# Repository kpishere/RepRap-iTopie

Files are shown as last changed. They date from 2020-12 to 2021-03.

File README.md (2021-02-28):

## Notes on this branch

I'm updating the build to accomodate parts readily available today.  Also making simplifications by design changes for ordering.

Changes include :  

- Pockets for screws that enable use of maximum 20mm screws (some were 30mm and these don't come in sets) 
- Adjust y-carrage to accommodate a 170mm x 170mm build heat plate screw hole pattern (heat plate is actually 235mm x 235mm)
- Adjust X,Y,Z sizes so that I only need 400mm rods and 400mm leadscrews (this was only 20mm or 40mm changes, why not that from beginning?)
- caviate: Notice that the Y-plane frame has pockets on one side and _should_ have the logo cut out on the other side but ... I'm not flipping this over to cut pockets, so the logo would be on the wrong side if it is cut like this.  Maybe don't cut the logo, rather 3D print it as a test and stick it on later if you want that.

A wiki page on the build milestones for the [iTopie400+](https://github.com/kpishere/RepRap-iTopie/wiki/General-RepRap-iTopie-build-experience-and-details-of-significance).

## [RepRap iTopie](http://reprap.org/wiki/ITopie)
Here you will find all the sources files for the [RepRap iTopie](http://reprap.org/wiki/ITopie).<br>The [build manual](http://reprap.org/wiki/ITopie_Build_Manual), [bill of materials](http://reprap.org/wiki/ITopie_Buyers_Guide) and other information is on the [RepRap wiki](http://reprap.org/wiki/ITopie).<br>Thank you.



## Highly customizable [frame generator](https://github.com/lautr3k/RepRap-iTopie/tree/dev/scad)

iTopie frame generator

## DXF [build tool](https://github.com/lautr3k/RepRap-iTopie/tree/dev/build)
Builder to create a clean layered DXF from (your custom) OpenSCAD source files.
iTopie DXF build tool
Generated DXF in CamBam

## Some pictures












## Looking for an extruder? Try the [Wade L3K Extruder](https://github.com/lautr3k/Wade-L3K).




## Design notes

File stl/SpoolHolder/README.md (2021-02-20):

Filler - The Customizable Filament Holder that fills your printer! by HugoHuge on Thingiverse: https://www.thingiverse.com/thing:3020026

The above release has been modified to use 5mm X 9 mm bearings (these are extra ones that come with a Titan Areo hot end assembly).

Cut parts have also been made if you wish to have two infil types in your print for those sections.

au: kpishere

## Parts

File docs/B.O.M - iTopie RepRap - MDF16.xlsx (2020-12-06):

Qty | Part name | Prix TTC (CHF) | Fournisseur
 | Wood
1 | MDF 16mm ~0.5m2 - Ex.: 860 x 580mm | 30 | Do-it (migro)
 | Wood screws
12 | 3.5 x 45mm | 1 | Bricovis
 | Metric screws
2 | M3 x 12mm |  | Bricovis
10 | M3 x 20mm |  | Bricovis
13 | M3 x 25mm |  | Bricovis
2 | M3 x 30mm |  | Bricovis
1 | M5 x 20mm |  | Bricovis
1 | M5 x 25mm | 8 | Bricovis
 | Washers
24 | M3 Washer - 3.2/7/0.5 |  | Bricovis
8 | M5 Washer - 5/8/1 |  | Bricovis
0 | M5 Washer - 5/12/0.5 | 3 | Bricovis | old version
 | Metric nuts
15 | M3 Nut |  | Bricovis
2 | M5 Nut - Nylock |  | Bricovis
2 | M8 Nut | 2 | Bricovis
 | Bearings
2 | 605ZZ Bearing | 2 | ebay
12 | LM8UU Linear bearing | 25 | reprapworld
 | Motor
5 | Nema17 - 1.8° / 4.8 kg/cm | 60 | reprapworld
 | Pulleys
2 | GT2 Pulley - 20 Theet | 8 | reprapworld
 | Belts
1 | GT2 Belt - 800mm | 5 | reprapworld
1 | GT2 Belt - 900mm | 5 | reprapworld
 | Flexible coupler
2 | 5/8mm Flexible coupler | 6 | reprapworld
 | Smooth rods
4 | D=8, L=380mm | 6 | reprapworld
2 | D=8, L=400mm | 3 | reprapworld
 | Threaded rods
2 | M8, L=360mm | 5 | Do-it (migro)
 | Electronics
1 | Smoothieboard 4XC | 130 | uberclock
1 | 30x30mm Fan | 3 | reprapworld
2 | 40x40mm Fan | 6 | reprapworld
1 | Power supply 12V - 30A | 25 | reprapworld
3 | Microswitch | 1.5 | conrad
1 | Heatbed MK3 | 20 | reprap.me
1 | Wiring | 10 | conrad
1 | Hotend Hexagone | 40 | reprapdiscount
 | Uncategorized
28 | Zip ties | 2 | conrad
 |  | TOTAL
 |  | 406.5

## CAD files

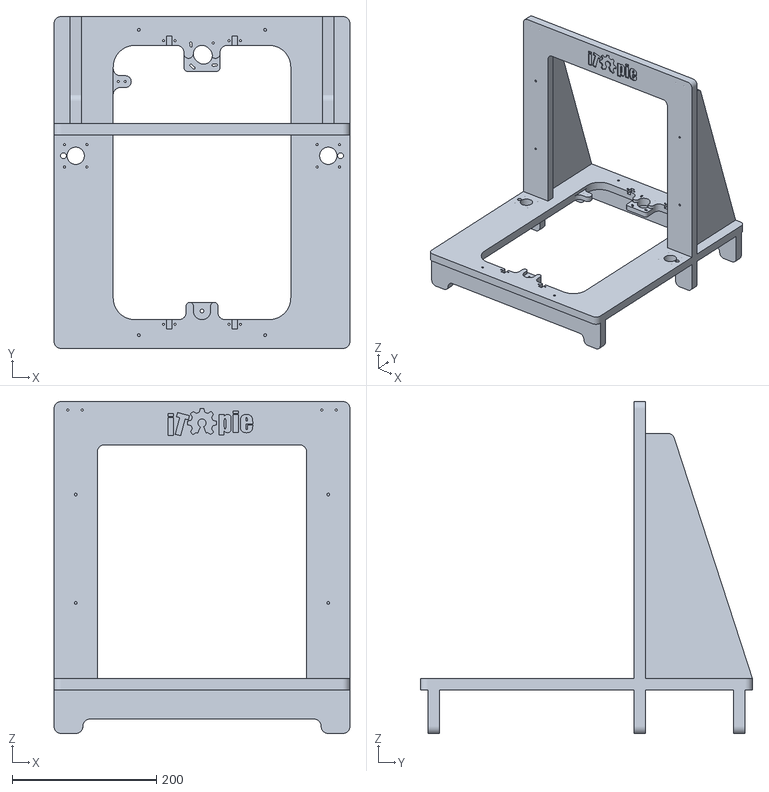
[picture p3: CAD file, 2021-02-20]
stl/main_assembled.stl
410.0 x 460.0 x 460.0

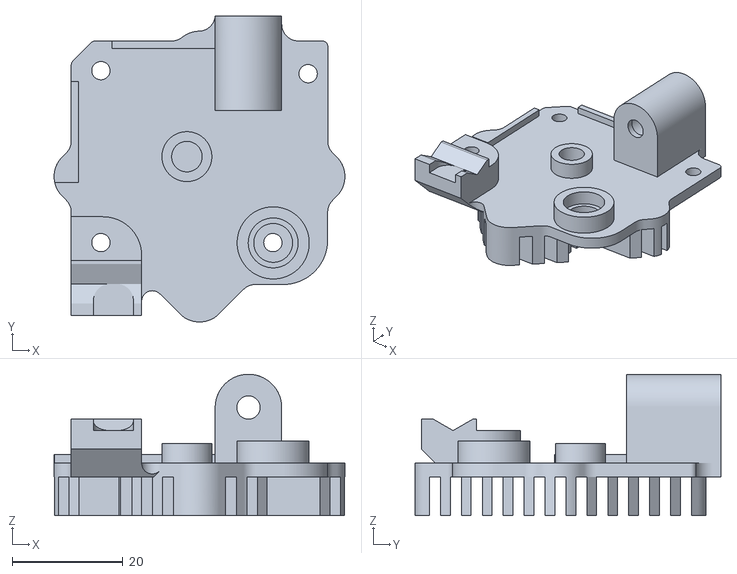
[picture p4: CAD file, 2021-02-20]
stl/Titan-Aero-Assembly_HotEnd.stl
52.4 x 55.2 x 25.5

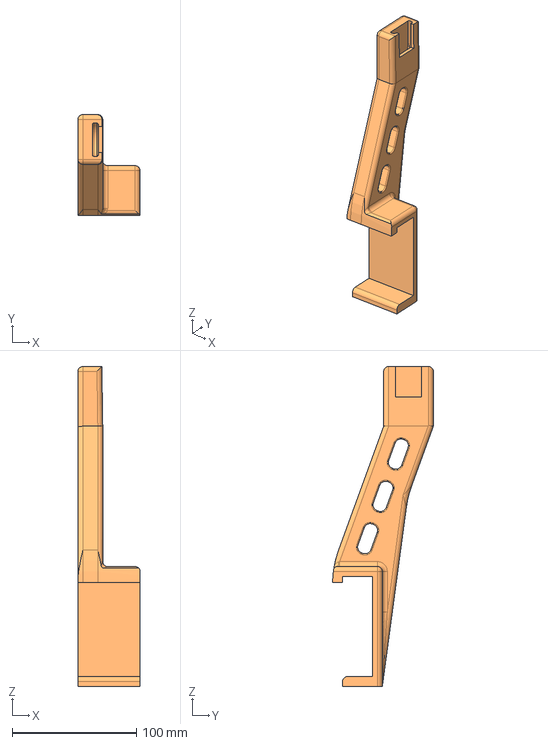
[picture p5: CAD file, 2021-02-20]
docs/Filler+-+The+Customizable+Filament+Holder+that+fills+your+printer!/files/FillerAnetA8Source.step
50.0 x 81.0 x 257.2 mm

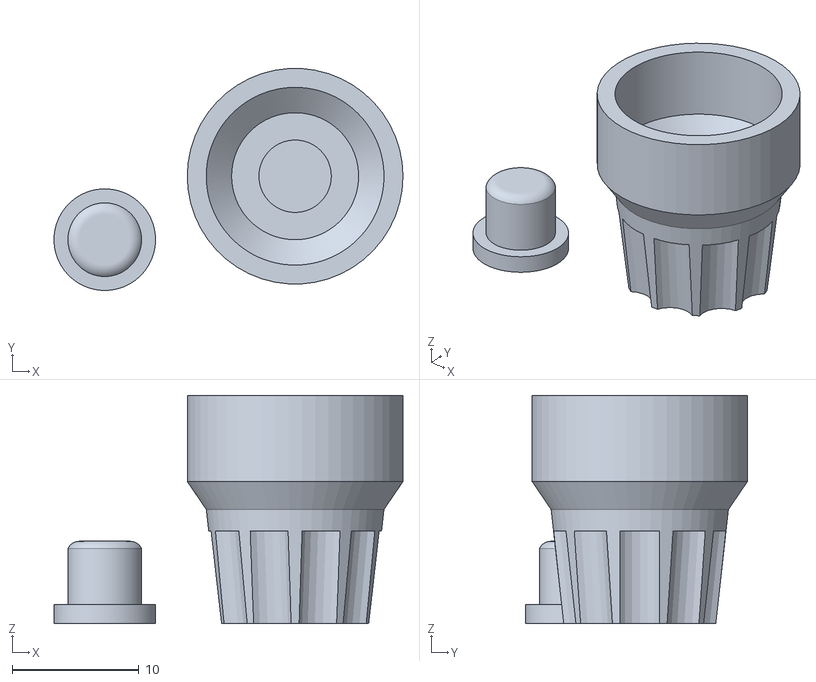
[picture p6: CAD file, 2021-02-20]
stl/AZSMZ 12864 Panel/Knob_v3.stl
27.5 x 17.5 x 18.0

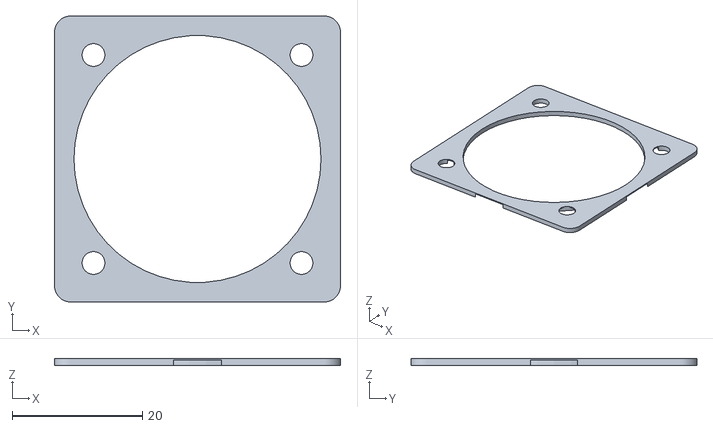
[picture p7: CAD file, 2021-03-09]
stl/damper_fan_mount.stl
44.0 x 44.0 x 1.00

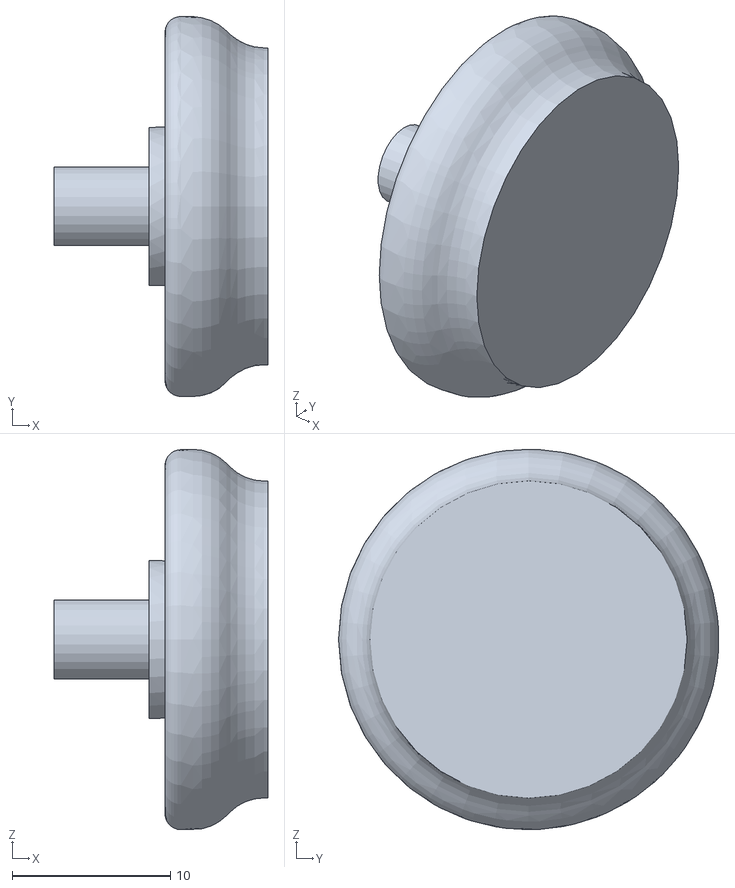
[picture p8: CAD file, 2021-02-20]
stl/SpoolHolder/SpoolRollerSection.stl
13.5 x 24.0 x 24.0

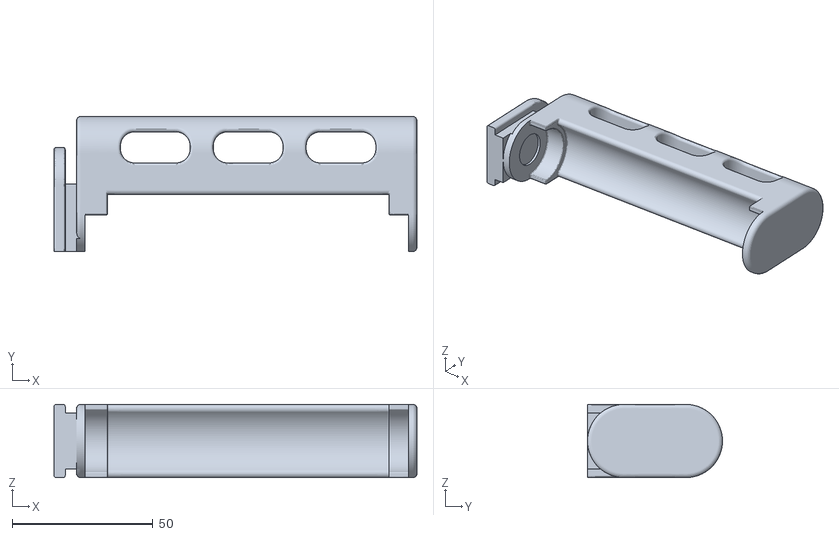
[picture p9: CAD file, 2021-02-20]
docs/Filler+-+The+Customizable+Filament+Holder+that+fills+your+printer!/3DPNFilHoldGuide.stl
129.0 x 48.0 x 26.0

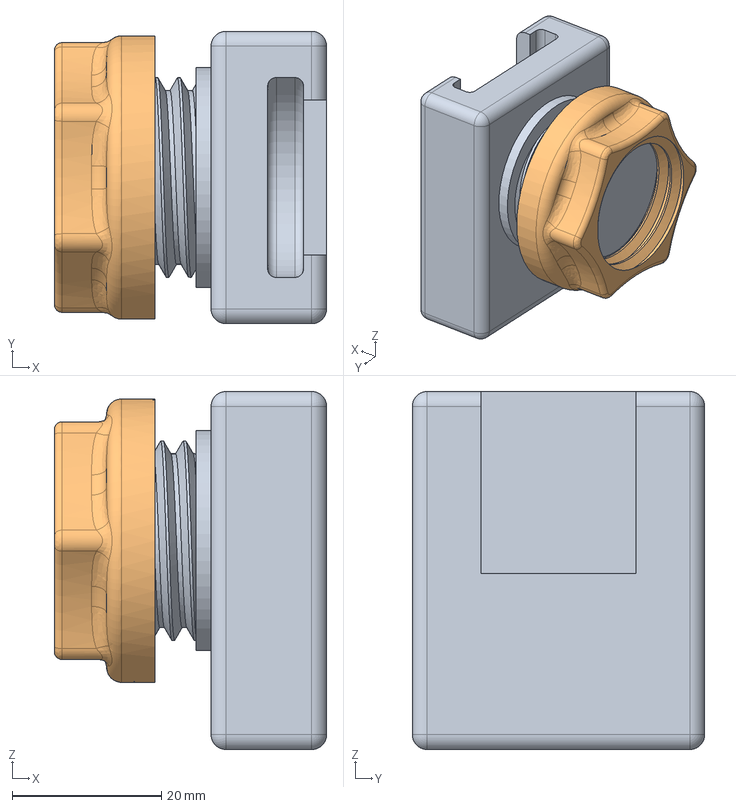
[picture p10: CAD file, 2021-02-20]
docs/Filler+-+The+Customizable+Filament+Holder+that+fills+your+printer!/files/FillerCR10-Ender3Source.step
36.5 x 39.2 x 48.0 mm

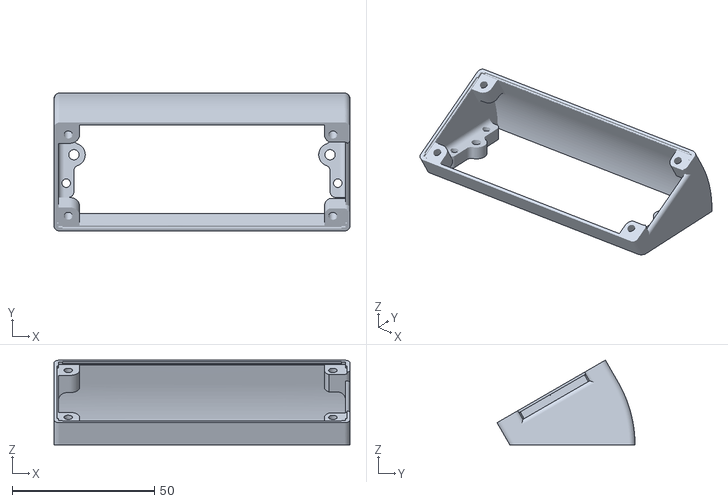
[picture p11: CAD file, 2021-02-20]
stl/AZSMZ 12864 Panel/Display_SD_Base.stl
104.0 x 48.5 x 29.8

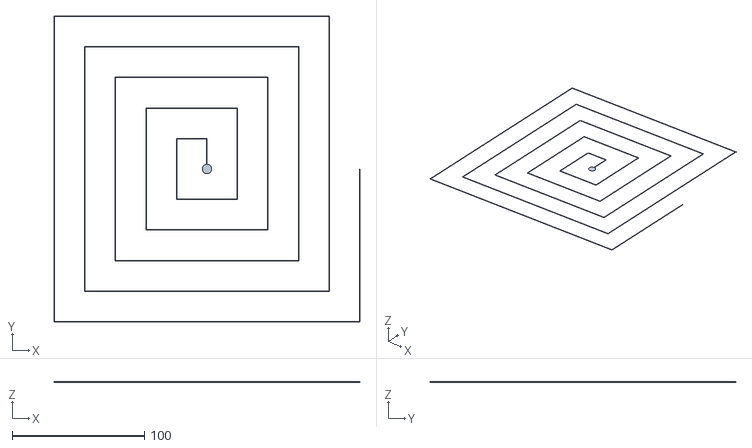
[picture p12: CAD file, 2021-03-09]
stl/bed_test.stl
231.2 x 231.2 x 0.2

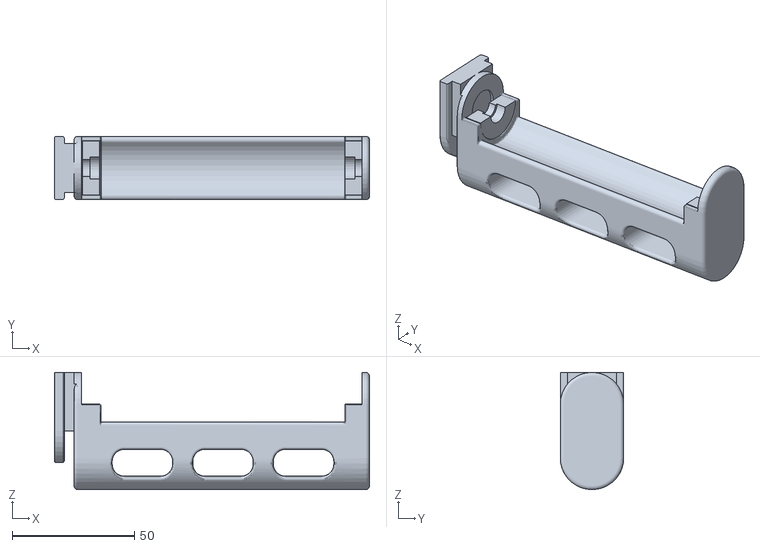
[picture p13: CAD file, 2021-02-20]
stl/SpoolHolder/SpoolBrace.stl
129.0 x 26.0 x 48.0

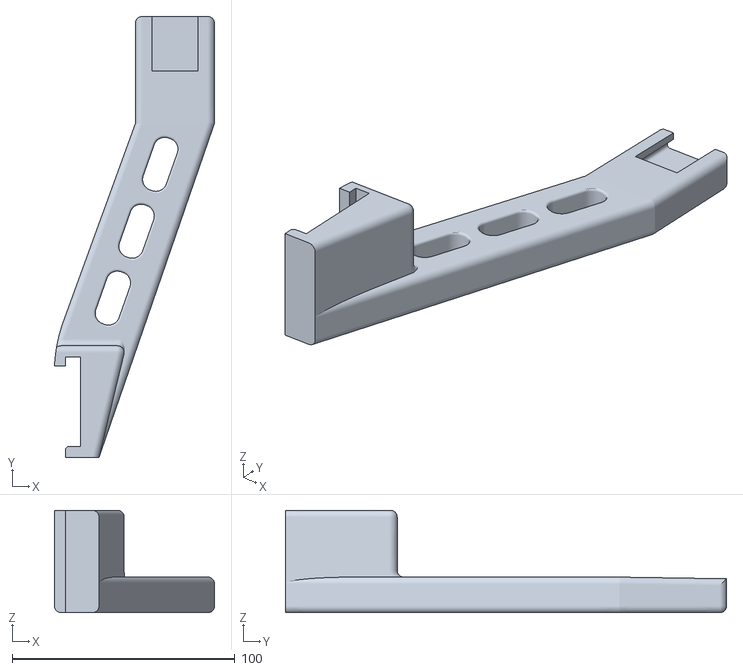
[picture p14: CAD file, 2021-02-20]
docs/Filler+-+The+Customizable+Filament+Holder+that+fills+your+printer!/FillerBracePrusaI3Mk1-2-3.stl
71.9 x 198.1 x 46.0

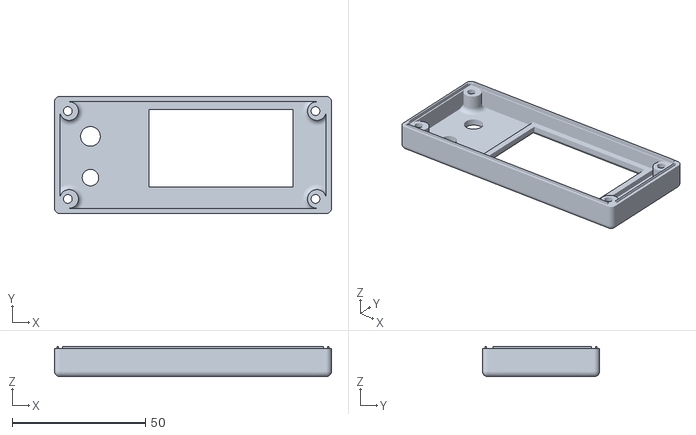
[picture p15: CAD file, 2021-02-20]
stl/AZSMZ 12864 Panel/Display_Front.stl
104.0 x 44.0 x 11.3

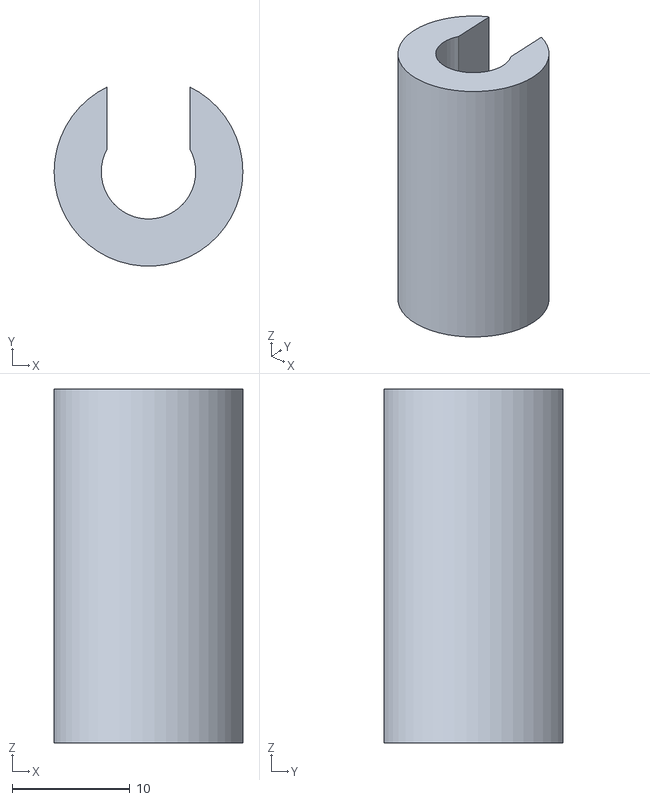
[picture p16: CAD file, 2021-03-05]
stl/clip-on-endstop-spacer.stl
16.0 x 15.2 x 30.0

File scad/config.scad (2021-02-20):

// iTopie RepRap - Configuration
//
// @version 1.0.1
// @license GPLv3
// @docs    http://reprap.org/wiki/ITopie  
// @sources https://github.com/lautr3k/RepRap-iTopie 
// @author  Sébastien Mischler <skarab>
// @author  http://www.onlfait.ch
//
$fn = 50;

// ---------------------------------------------------------------- //
// output settings
// ---------------------------------------------------------------- //
// output version
// 0 : CNC milling (default)
// 1 : Laser cutting
output_version = 0;

// output mode
// 0 : 2D preview (default)
// 1 : extruded view (slow)
// 2 : export first layer (plates)
// 3 : export second layer (pockets)
// 4 : build preview (slow)
output_mode = 0;

// output type
// 0 : all parts
// 1 : plate 1 (horizontal_plate, y_carriage, feet)
// 2 : plate 2 (vertical_plate, triangles, feet)
// 3 : horizontal_plate
// 4 : vertical_plate
// 5 : y_carriage
// 6 : triangle
// 7 : feet
output_type = 0;

// parts margin (mode : 0-3)
parts_margin = 10;

// ---------------------------------------------------------------- //
// drawing settings
// ---------------------------------------------------------------- //
sheet_thickness = 16;                    // raw sheet thickness
pockets_depth   = 6;                     // pockets depth
pockets_color   = "RoyalBlue";           // pockets color
connector_size  = [20, sheet_thickness]; // pockets/fingers [width, height]

// ---------------------------------------------------------------- //
// shortcuts
// ---------------------------------------------------------------- //
m3_screw_radius = 1.5;
m4_screw_radius = 2;
m4_washer_radius = 4;
workpiece_x = 1220;
workpiece_y = 610;

// ---------------------------------------------------------------- //
// horizontal plate
// ---------------------------------------------------------------- //
horizontal_plate_width         = 410;              // 
horizontal_plate_height        = 460;              // 
horizontal_plate_borders       = [40, 82, 40, 82]; // borders weight       [top, right, bottom, left]
horizontal_plate_outer_corners = [10, 10, 10, 10]; // outer corners radius [topLeft, topRight, bottomRight, bottoLeft]
horizontal_plate_inner_corners = [30, 30, 30, 30]; // inner corners radius [topLeft, topRight, bottomRight, bottoLeft]

// y motor mount
y_motor_mount_width   = 50;              //
y_motor_mount_height  = 36;              //
y_motor_mount_corners = [5, 5, 10, 10];  // corners radius [topLeft, topRight, bottomRight, bottoLeft]
y_motor_mount_angle   = 8;               // motor rotation angle (belt tensionner) 0 = disabled
y_motor_holes_radius  = m3_screw_radius; // y motor screw holes radius

// z_motor mount
z_motor_mount_margin  = 8;     // between the "motor" and the "z_plate" (border to border)
z_motor_mount_spacing = undef; // between the two motor mount (axis to axis) [undef = auto]

z_motor_holes_radius = m3_screw_radius; // z motor screw holes radius

// z rods
z_rod_spacing = 17; // between the "motor" and the "z rod" (axis to axis)
z_rod_radius  = 4;  // z smoothe rod radius

z_rod_holder_holes_radius  = m3_screw_radius; // z rod top holder holes radius
z_rod_holder_holes_margin  = [12, 6];         // [from the top frame border, between the z rod and the first holder hole (axis to axis)]
z_rod_holder_holes_spacing = 20;              // between the two holder holes (axis to axis)

// y idler mount
y_idler_mount_width       = 44;             //
y_idler_mount_height      = 24;             //
y_idler_mount_corners     = [5, 5, 10, 10]; // corners radius [topLeft, topRight, bottomRight, bottoLeft]
y_idler_mount_hole_radius = 2.5;            // y idler bearing hole radius

// y idler pocket
y_idler_pocket_width   = undef;                 // idler pocket width [undef = auto]
y_idler_pockets_height = y_idler_mount_height;  // idler pocket height

// y endstop mount
y_endstop_mount_width    = 25;                 //
y_endstop_mount_height   = 16.4;               //
y_endstop_mount_corners  = [8.2, 8.2, 10, 10]; // corners radius [topLeft, topRight, bottomRight, bottoLeft]
y_endstop_mount_position = 82;                 // from the frame top border to the endstop top border

// ---------------------------------------------------------------- //
// vertical plate
// ---------------------------------------------------------------- //
// vertical plate
vertical_plate_width         = horizontal_plate_width;  // outer width
vertical_plate_height        = horizontal_plate_height; // outer height
vertical_plate_borders       = [60, 60, undef, 60];     // borders weight       [top, right, bottom, left]
vertical_plate_outer_corners = [10, 10, 10, 10];        // outer corners radius [topLeft, topRight, bottomRight, bottoLeft]
vertical_plate_inner_corners = [10, 10, 10, 10];        // inner corners radius [topLeft, topRight, bottomRight, bottoLeft]
vertical_plate_position      = undef;                   // y position from the horizontal plate bottom border      

// ---------------------------------------------------------------- //
// logo
// ---------------------------------------------------------------- //
dxf_logo   = "logo.dxf"; // path to DXF logo
logo_depth = 2;          // logo pocket depth (set to undef for through cut)


// ---------------------------------------------------------------- //
// rear triangles
// ---------------------------------------------------------------- //
triangle_width  = undef;               // rear triangle width         [undef = auto]
triangle_height = undef;               // rear triangle height        [undef = auto]
triangle_angle  = undef;               // rear triangle angle         [undef = auto]
triangle_margin = [undef, 15, 15, 15]; // rear triangle margin        [top, right, bottom, left]
triangle_radius = 10;                  // rear triangle corner radius [undef = auto]

triangle_connectors_size   = [connector_size[1], connector_size[0]]; // rotate 90°
triangle_connectors_margin = [63, 22, undef, 22];                    // pockets margin [top, right, ---, left]

triangle_holes_radius = m4_screw_radius; // screws holes radius
triangle_holes_margin = 20;              // screws margin (from z triangle pocket border)

// ---------------------------------------------------------------- //
// y carriage
// ---------------------------------------------------------------- //
y_carriage_corners_holes_spacing = [170, 170];      // [x, y] axis to axis
y_carriage_outer_offset          = [11, 11];        // [x, y]
y_carriage_holes_radius          = m4_screw_radius; //
y_carriage_ergots_radius         = 5.5;             //
y_carriage_triangle_offset       = 10;              // inner offset
y_carriage_triangle_margin       = [11, 11];        // [x, y]
y_carriage_thumbwheel_radius     = 10;

y_carriage_belt_holder_offset        = 6;     // offset position from y carriage axis (issue#13)
y_carriage_belt_holder_screw_spacing = 16;    // y belt holder holes spacing (axis to axis) 
y_carriage_lm8_holder_screw_spacing  = 24;    // y lm8uu holder holes spacing (axis to axis) 
y_carriage_lm8_holder_vspacing       = undef; // lm8uu holder vertical spacing (axis to axis)

y_rod_pockets_size = [8, 13];         // pockets size   [rod diameter, length]
y_rod_spacing      = undef;           // pockets spacing (axis to axis) [undef = auto]
y_rod_holes_radius = m3_screw_radius; // y rod screws holes radius
y_rod_holes_margin = 4;               // y rod screws margin (from y rod pocket border)

y_endstop_holes_radius  = m3_screw_radius; // endstop screws holes radius
y_endstop_holes_spacing = 9.5;             // between the two endstop screws (axis to axis)

// ---------------------------------------------------------------- //
// feet
// ---------------------------------------------------------------- //
feet_width      = horizontal_plate_width;  // 
feet_height     = 60;                      // 
feet_corners    = [10, 10, 10, 10];        // corners radius [leftOut, leftIn, rightIn, rightOut]
feet_gap_height = 20;                      // gap height ?

feet_connectors_size   = connector_size;       //
feet_connectors_margin = [10.5, 40, 10.5, 40]; // pockets margin [top, right, bottom, left]

feet_holes_radius = m4_screw_radius; // feet screws holes radius
feet_holes_margin = 10;              // feet screws horizontal margin (for fine adjustement)

foot_width = 40; //

// ---------------------------------------------------------------- //
//     CHANGE NOTHING BELOW, UNLESS YOU KNOW WHAT YOU ARE DOING
// ---------------------------------------------------------------- //

// ---------------------------------------------------------------- //
// pockets
// ---------------------------------------------------------------- //
pockets_height = sheet_thickness - pockets_depth;
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

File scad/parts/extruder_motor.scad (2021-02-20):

$fn = 50;

use <threadlib/threadlib.scad>;

MY_THREAD_TABLE = [
    ["M19-ext", [2.25, 8.3120, 16.9380, [[0, -1.0929], [0, 1.0929], [1.5830, 0.1790], [1.5830, -0.1790]]]],
    ["M19-int", [2.25, -10.2925, 20.2925, [[0, 1.2304], [0, -1.2304], [1.5330, -0.3453], [1.5330, 0.3453]]]]
];

baseplate_thickness=5;
baseplate_xy_len=42;
baseplate_corner_rad=3;

baseplate_mount_rad=2; // m4
baseplate_mount_xy_len=31;
baseplate_center_rad=12;

bushing_internal_len=27;
bushing_wall_thickness=3;
bushing_opening_rad=5;
bushing_access_rad=4;
bushing_chamfer_len=1.5;

insert_len=50;
insert_rad=4;
insert_shaft_len=20;
insert_shaft_rad=2.51;
insert_flex_len=25;
insert_flex_xy=2.6;

thru_m4=4.1/2;

// motor mount & z rod pockets
// 0 = none, 1 = left, 2 = right
module motor_mount_holes(radius) {
    circle(radius);
    translate([baseplate_mount_xy_len, 0, 0])
        circle(radius);
    translate([baseplate_mount_xy_len, baseplate_mount_xy_len, 0])
        circle(radius);
    translate([0, baseplate_mount_xy_len, 0])
        circle(radius);
    translate([baseplate_mount_xy_len/2, baseplate_mount_xy_len/2, 0]) {
        circle(baseplate_center_rad);
    }
}

module adapter() {
    // baseplate
    linear_extrude(baseplate_thickness) {
        difference() {        
            translate([-2*baseplate_mount_rad,-2*baseplate_mount_rad]) {
                minkowski() {
                    square([baseplate_xy_len-baseplate_corner_rad,baseplate_xy_len-baseplate_corner_rad]);
                    circle(baseplate_corner_rad);
                }
            }
            motor_mount_holes(baseplate_mount_rad);
        }
    };
    
    // mount
    difference() {
        union() {
            linear_extrude(baseplate_thickness+bushing_internal_len) {
                translate([-2*baseplate_mount_rad,baseplate_xy_len-2*baseplate_mount_rad]) square([baseplate_xy_len-2*baseplate_mount_rad,baseplate_thickness]);
                translate([baseplate_mount_xy_len/2-baseplate_thickness/2,baseplate_corner_rad+baseplate_mount_rad+2*baseplate_center_rad]) square([baseplate_thickness,baseplate_xy_len/2-baseplate_center_rad]);
            }
            // boss mount left
            translate([-bushing_access_rad,baseplate_xy_len-2*baseplate_mount_rad,baseplate_thickness+bushing_internal_len-baseplate_thickness])
            rotate([0,90,90])
            linear_extrude(baseplate_thickness) circle(baseplate_thickness);
            // boss mount right
            translate([baseplate_mount_xy_len+baseplate_corner_rad,baseplate_xy_len-2*baseplate_mount_rad,baseplate_thickness+bushing_internal_len-baseplate_thickness])
            rotate([0,90,90])
            linear_extrude(baseplate_thickness) circle(baseplate_thickness);
        }
        // mount hole left
        translate([-bushing_access_rad,baseplate_xy_len-2*baseplate_mount_rad,baseplate_thickness+bushing_internal_len-baseplate_thickness])
        rotate([0,90,90])
        linear_extrude(baseplate_thickness) circle(thru_m4);
        // mount hole right
        translate([baseplate_mount_xy_len+baseplate_corner_rad,baseplate_xy_len-2*baseplate_mount_rad,baseplate_thickness+bushing_internal_len-baseplate_thickness])
        rotate([0,90,90])
        linear_extrude(baseplate_thickness) circle(thru_m4);
    }
    // insert
    translate([baseplate_mount_xy_len/2, baseplate_mount_xy_len/2,0])
    difference() {
        cylinder(insert_len,r1=insert_rad, r2=insert_rad);
        // stepper shaft
        translate([0,0,-.1])
        difference() {
            cylinder(insert_shaft_len,r1=insert_shaft_rad, r2=insert_shaft_rad);
            translate([-insert_shaft_rad,insert_shaft_rad-0.5,-0.1])
            cube([2*insert_shaft_rad,2*insert_shaft_rad,insert_shaft_len]);
        }
        // flex cable shaft
        translate([-insert_flex_xy/2,-insert_flex_xy/2,insert_len-insert_flex_len+0.1])
        cube([insert_flex_xy,insert_flex_xy,insert_flex_len]);
    }
    
    // coupler housing
    translate([baseplate_mount_xy_len/2, baseplate_mount_xy_len/2, baseplate_thickness])
        difference() {
            union() {
                cylinder(bushing_internal_len+bushing_wall_thickness-bushing_chamfer_len,r1=baseplate_center_rad+bushing_wall_thickness
                , r2=baseplate_center_rad+bushing_wall_thickness);
                translate([0,0,bushing_internal_len+bushing_wall_thickness-bushing_chamfer_len])
                cylinder(bushing_chamfer_len,r1=baseplate_center_rad+bushing_wall_thickness, r2=baseplate_center_rad+bushing_wall_thickness-bushing_chamfer_len);
            }
            cylinder(bushing_internal_len+bushing_wall_thickness+2
                ,r1=bushing_opening_rad, r2=bushing_opening_rad);   
            translate([0,0,-0.5])
                cylinder(bushing_internal_len+1,r1=baseplate_center_rad, r2=baseplate_center_rad);      
     
            
         // access holes
    translate([-baseplate_mount_xy_len/2,0, 1+bushing_access_rad])
        rotate([0,90,0])
        cylinder(50,r1=bushing_access_rad,r2=bushing_access_rad);
    translate([-baseplate_mount_xy_len/2,0, 24-bushing_access_rad])
        rotate([0,90,0])
        cylinder(50,r1=bushing_access_rad,r2=bushing_access_rad);
       
    }

    // thread extension
    translate([baseplate_mount_xy_len/2, baseplate_mount_xy_len/2, baseplate_thickness+bushing_internal_len+bushing_wall_thickness])
        difference() {
            bolt("M19", turns=5, table=MY_THREAD_TABLE);
            translate([0,0,-5])
            cylinder(30,r1=bushing_opening_rad,r2=bushing_opening_rad);
        }
        
}

module adapter_xsection() {
    difference() {
        adapter();
            translate([baseplate_mount_xy_len/2, baseplate_mount_xy_len/2,0]) 
                cube([100,100,100]);
    }
}

//adapter_xsection();
adapter();

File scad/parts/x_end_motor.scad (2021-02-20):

include <../config.scad>
include <../shapes.scad>
include <Round-Anything/polyround.scad>

// motor pivot point mount 1
motor_piv1=37.5;
motor_piv2=pully_offset2-motor_mount_ctr_spc/2;
motor_piv_dia=3.6;
motor_piv_boss_dia=motor_piv_dia+8;

// motor mount 2
motor_mnt_dia21=2*(motor_mount_ctr_spc-motor_piv_dia/2);
motor_mnt_dia22=motor_mnt_dia21+motor_piv_dia*2;
motor_mnt21=motor_piv1;
motor_mnt22=motor_piv2+motor_mount_ctr_spc;
motor_mnt2_th1=270-8;
motor_mnt2_th2=motor_mnt2_th1+8;

// motor mount 3
motor_mnt_dia31=2*(sqrt(2)*motor_mount_ctr_spc-motor_piv_dia/2);
motor_mnt_dia32=motor_mnt_dia31+motor_piv_dia*2;
motor_mnt31=1+motor_piv1-(motor_mnt_dia31+motor_piv_dia)/2/sqrt(2);
motor_mnt32=2.2+motor_piv2+(motor_mnt_dia31+motor_piv_dia)/2/sqrt(2);
motor_mnt3_th1=270+45-8;
motor_mnt3_th2=motor_mnt3_th1+10;

// motor axis offset
motor_axis_dia1=2*(sqrt(2)*motor_mount_ctr_spc/2-(motor_boss_dia+1)/2);
motor_axis_dia2=motor_axis_dia1+(motor_boss_dia+1)*2;
motor_axis_ang1=315-8;
motor_axis_ang2=motor_axis_ang1+8;

// wall geometry
platePoints = [
    [0,0,0], //1
    [xbar_offset,0,0], //2
    [xbar_offset,end_motor_width,0],//3
    [motor_mount_ctr_spc,end_motor_width,5],//4
    [motor_mount_ctr_spc,end_motor_width-motor_mount_ctr_spc/2,0],//5 - curve edge
    [motor_mount_ctr_spc+3,end_motor_width-20,0],//6
    [motor_mount_ctr_spc+2.4,end_motor_width-30,0],//6.1
    [motor_mount_ctr_spc-motor_piv2,end_motor_width-35.5,0],//7
    [9+motor_piv2,end_motor_width-13.8-8.1-17+7.6,0],//8
    [0,end_motor_width-31.3,0],//9
];

// end idler wall assembly
module end_motor_wall(thickness, pos, hole_clear=false) {
    translate(pos)
    rotate([0,90,0]) 
    linear_extrude(height = thickness,  convexity = 1 )
    difference() {
        union() {
            translate([0,-end_motor_width,0]) {
                shell2d(-4) {
                    polygon(
                        polyRound(platePoints,30)
                    );
                    translate([motor_piv2,7]) gridpattern(memberW = 2, sqW = 8, iter = 15, r = 1);                    
                }
            }                        
            // motor mount 1 pivot
            translate([motor_piv2,-motor_piv1]) {
                bushing(motor_piv_dia,motor_piv_boss_dia);
            }
            // motor mount boss 2 
            translate([motor_mnt22,-motor_mnt21-2]) {
                bushing(0,motor_piv_boss_dia+2);
            }            
            // motor mount boss 3 
            translate([motor_mnt32,-motor_mnt31-2]) {
                bushing(0,motor_piv_boss_dia);
            }            
        }
        // clearance for motor axis and mounts
        translate([motor_piv2,-motor_piv1]) {
            // motor axis
            slot_curved(motor_axis_dia1,motor_axis_dia2,motor_axis_ang1,motor_axis_ang2);
            // motor mount 2 slot
            slot_curved(motor_mnt_dia21,motor_mnt_dia22,motor_mnt2_th1,motor_mnt2_th2);
            // motor mount 3 slot
            slot_curved(motor_mnt_dia31,motor_mnt_dia32,motor_mnt3_th1,motor_mnt3_th2);
        }
        // clearence for bushing mount holes
        if(hole_clear) 
            translate([xbar_offset-zscrew_boss_dia+6,2-end_motor_width]) 
            square([zscrew_boss_dia,2+zscrew_boss_height/2]);
    }
}


// End Idler - x-axis bar along y-axis, origin right-hand centre of lower x-bar
module end_motor() {
    // X-axis bars
    difference() {
        rotate([90,0,0])
        union() {
            translate([0,0,xbar_offset])
            linear_extrude(height = end_motor_width-end_idler_width+1,  convexity = 1 )
                sleeve(rod_dia,end_boss_dia);
            linear_extrude(height = end_motor_width-(end_motor_width-end_idler_width+1.1),  convexity = 1 )
                bushing(0,end_boss_dia);
            translate([0,0,31.3])
            linear_extrude(height = end_motor_width-31.3,  convexity = 1 ) 
                translate([0,xbar_offset]) sleeve(rod_dia,end_boss_dia);        
        }
        translate([-rod_dia,-end_motor_width-1,-11]) cube([end_boss_dia,end_motor_width+2,5]);       
        // chamfer
        translate([0,-end_motor_width-.5,0]) 
            rotate([-90,0,0])
                cylinder(1,d1=rod_dia+2,d2=rod_dia);
        translate([0,-end_motor_width-.5,xbar_offset]) 
            rotate([-90,0,0])
                cylinder(1,d1=rod_dia+2,d2=rod_dia);
        
        // inside clearence for z-bar
        translate([-13.9,-end_motor_width+zboss_dia/2+zscrew_zbar_offset, -6]) 
                linear_extrude(height = xbar_offset-.5,  convexity = 1 )
                    rotate([0,0,135])
                        sleeve(1,lmuu_dia);        

        // inside clearence for z-screw mount holes
        translate([-13.9,-end_motor_width+zboss_dia/2,-6])
        linear_extrude(height = zscrew_boss_height,  convexity = 1 ) {             
            // Bushing holes
            rotate([0,0,45]) {
                translate([zscrew_bushing_mount_hole_offset,0,0]) circle(d=m3_drill4tap_dia);
                translate([-zscrew_bushing_mount_hole_offset,0,0]) circle(d=m3_drill4tap_dia);
                translate([0,zscrew_bushing_mount_hole_offset,0]) circle(d=m3_drill4tap_dia);
                translate([0,-zscrew_bushing_mount_hole_offset,0]) circle(d=m3_drill4tap_dia);
            }
        }
        
        // inside clearence for motor mount holes and slots        
        translate([end_boss_dia/2-end_boss_dia,0,xbar_offset])
            rotate([0,90,0]) 
            linear_extrude(height = end_boss_dia,  convexity = 1 )
            // motor mount 
            translate([motor_piv2,-motor_piv1]) {
                // clearance for motor axis
                slot_curved(motor_axis_dia1,motor_axis_dia2,motor_axis_ang1,motor_axis_ang2);
                // pivot 1
                bushing(0,motor_piv_dia);
                // slot 2
                slot_curved(motor_mnt_dia21,motor_mnt_dia22,motor_mnt2_th1,motor_mnt2_th2);
                // slot 3
                slot_curved(motor_mnt_dia31,motor_mnt_dia32,motor_mnt3_th1,motor_mnt3_th2);
            }
        
        // clearence for x-axis motor tensioning screw
        translate([0,-motor_piv1+motor_mnt_dia31/2-11.3,xbar_offset-motor_piv2-motor_mnt_dia31/2+11.3])
            rotate([135,0]) {
                linear_extrude(height = 25,  convexity = 1 )              
                    bushing(0,m3_drill4tap_dia);
                translate([0,0,15])
                linear_extrude(height = 10,  convexity = 1 )              
                    bushing(0,m3_drill4tap_dia+4);
            }
    }

    // Z-screw bushing
    translate([-13.9,-end_motor_width+zboss_dia/2,-6])
    difference() {
        linear_extrude(height = zscrew_boss_height,  convexity = 1 ) {             
            //rotate(180)
            difference() {
                bushing(zscrew_dia, zscrew_boss_dia);
                // side hole clearence
                translate([0,19,0]) bushing(zscrew_dia, zscrew_boss_dia);
                // Inside clerence
                translate([zscrew_boss_dia/2-2,-zscrew_boss_dia/2,0]) square([2,zscrew_boss_dia]);
                // Bushing holes
                rotate([0,0,45]) {
                    translate([zscrew_bushing_mount_hole_offset,0,0]) circle(d=m3_drill4tap_dia);
                    translate([-zscrew_bushing_mount_hole_offset,0,0]) circle(d=m3_drill4tap_dia);
                    translate([0,zscrew_bushing_mount_hole_offset,0]) circle(d=m3_drill4tap_dia);
                    translate([0,-zscrew_bushing_mount_hole_offset,0]) circle(d=m3_drill4tap_dia);
                }
            }
        }
        // chamfer
        translate([0,0,-.5]) cylinder(1,d1=zscrew_dia+2,d2=zscrew_dia);
    }
    
    
    // side walls
    end_motor_wall(wall_thickness,[end_boss_dia/2-wall_thickness,0,xbar_offset]);    
    difference() {
        end_motor_wall(wall_thickness,[-end_boss_dia/2,0,xbar_offset],hole_clear=true);
        // inside clearence for z-bar
        translate([-13.9,-end_motor_width+zboss_dia/2+zscrew_zbar_offset, -6]) 
                linear_extrude(height = xbar_offset-.5,  convexity = 1 )
                    rotate([0,0,45])
                        sleeve(1,lmuu_dia);
    }
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

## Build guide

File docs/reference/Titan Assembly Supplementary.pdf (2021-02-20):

# ASSEMBLY OVERVIVEW

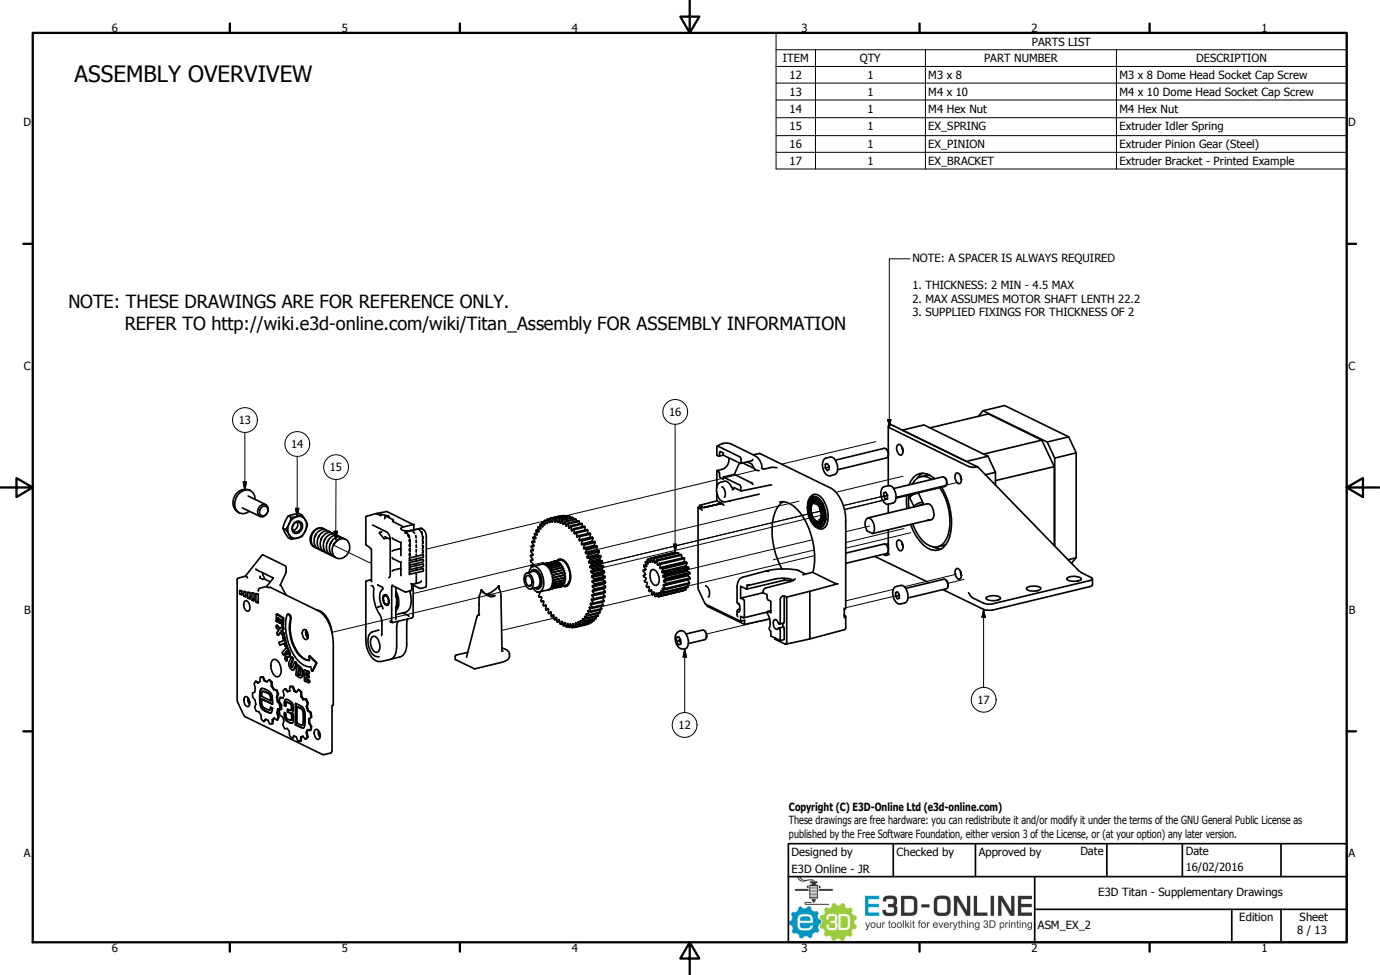
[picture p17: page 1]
PARTS LIST; ITEM; QTY; PART NUMBER; DESCRIPTION; M3 x 8 Dome Head Socket Cap Screw; M4 x 10 Dome Head Socket Cap Screw; M4 Hex Nut; EX_SPRING; Extruder Idler Spring; EX_PINION; Extruder Pinion Gear (Steel); EX_BRACKET; Extruder Bracket - Printed Example; ASM_EX_2; E3D Online - JR; Designed by; Checked by; Approved by; Date; Edition; Sheet

NOTE: A SPACER IS ALWAYS REQUIRED

1. THICKNESS: 2 MIN - 4.5 MAX
2. MAX ASSUMES MOTOR SHAFT LENTH 22.2
3. SUPPLIED FIXINGS FOR THICKNESS OF 2

NOTE: THESE DRAWINGS ARE FOR REFERENCE ONLY.

REFER TO http://wiki.e3d-online.com/wiki/Titan_Assembly FOR ASSEMBLY INFORMATION

Copyright (C) E3D-Online Ltd (e3d-online.com)
These drawings are free hardware: you can redistribute it and/or modify it under the terms of the GNU General Public License as
published by the Free Software Foundation, either version 3 of the License, or (at your option) any later version.

E3D Titan - Supplementary Drawings

# ASSEMBLY STEPS 1-4

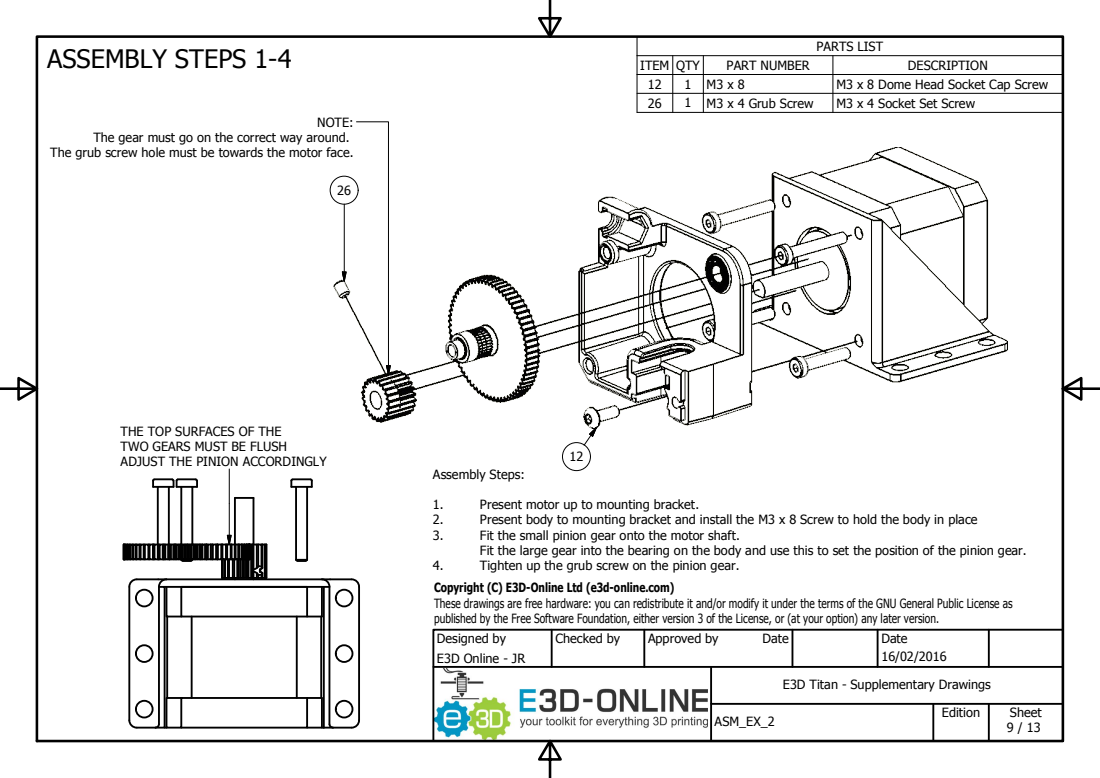
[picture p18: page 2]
ITEM; QTY; PART NUMBER; DESCRIPTION; M3 x 8 Dome Head Socket Cap Screw; M3 x 4 Grub Screw; M3 x 4 Socket Set Screw; E3D Online - JR; Designed by; Checked by; Approved by; Date; Edition; Sheet; Assembly Steps:; NOTE:

The gear must go on the correct way around.

The grub screw hole must be towards the motor face.

THE TOP SURFACES OF THE
TWO GEARS MUST BE FLUSH
ADJUST THE PINION ACCORDINGLY

1. Present motor up to mounting bracket.
2. Present body to mounting bracket and install the M3 x 8 Screw to hold the body in place
3. Fit the small pinion gear onto the motor shaft.

Fit the large gear into the bearing on the body and use this to set the position of the pinion gear.

4. Tighten up the grub screw on the pinion gear.
Copyright (C) E3D-Online Ltd (e3d-online.com)
These drawings are free hardware: you can redistribute it and/or modify it under the terms of the GNU General Public License as
published by the Free Software Foundation, either version 3 of the License, or (at your option) any later version.

E3D Titan - Supplementary Drawings

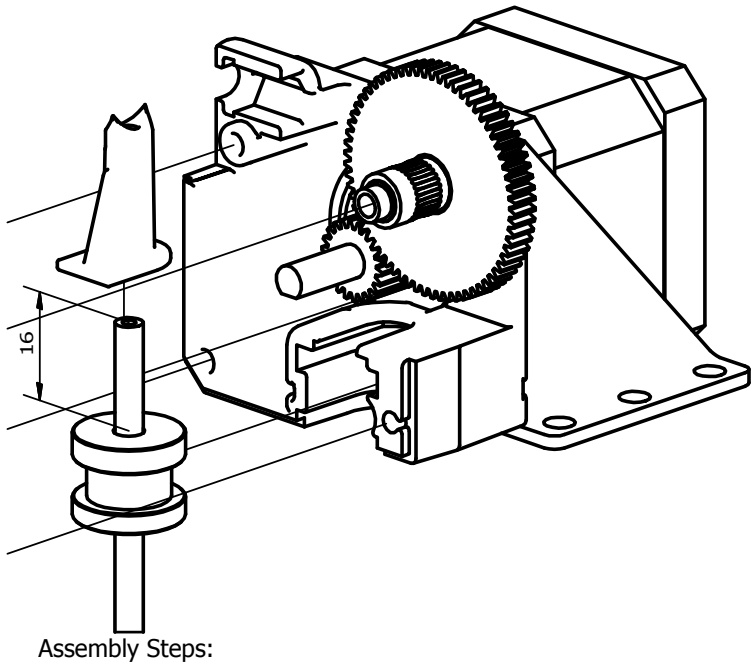
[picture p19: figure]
Assembly Steps:

ITEM | QTY | PART NUMBER | DESCRIPTION
14 | 1 | M4 Hex Nut | M4 Hex Nut
13 | 1 | M4 x 10 | M4 x 10 Dome Head Socket Cap Screw
27 | 1 | PTFE

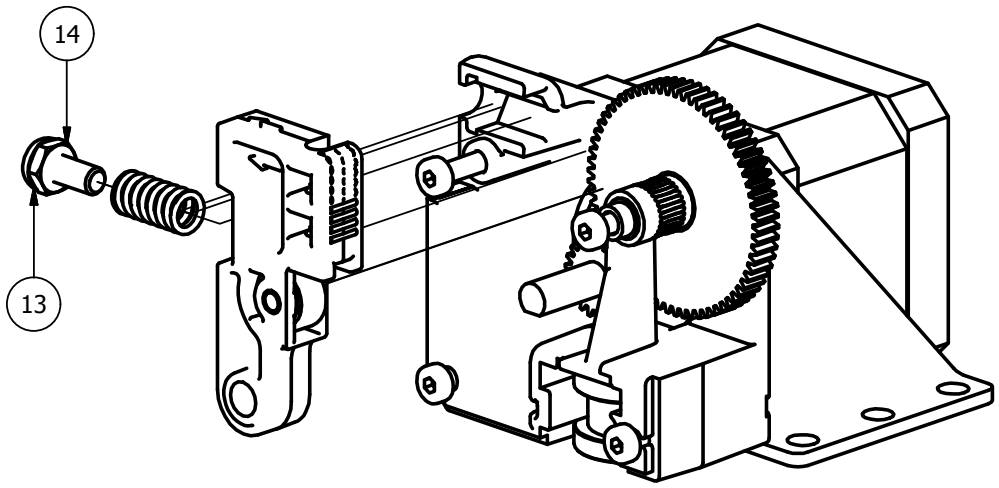
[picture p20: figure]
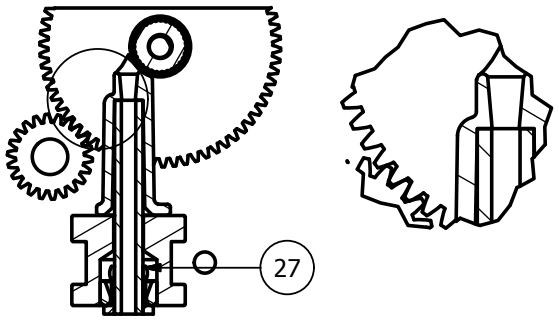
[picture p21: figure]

E3D Titan - Supplementary Drawings

E3D Online - JR | 16/02/2016
Designed by | Checked by | Approved by | Date
Edition | Sheet

Date

Copyright (C) E3D-Online Ltd (e3d-online.com)
These drawings are free hardware: you can redistribute it and/or modify it under the terms of the GNU General Public License as published by the Free Software Foundation, either version 3 of the License, or (at your option) any later version.
5. Install the filament guide and HotEnd into the extruder body. For the 1.75mm version, make sure the PTFE goes all the way up into the filament guide. See cutout below.
Rotate the HotEnd if necessary to insert.

Note: The diagram shows a bowden adaptor for a bowden setup,
if you are using a direct, there will be a HotEnd in place of this part.

Assembly Steps:

6. Slide the lever onto the motor shaft.
7. Screw the M4 Nut fully onto the M4 x 10 Screw
8. Slide the spring onto the screw and insert the assembly into the slot as shown.

Note: This bit is fiddly. Don't add any tension to the spring,
it will fly across the room to be lost forever.

# ASSEMBLY STEPS 5-8

# ASSEMBLY STEP 9

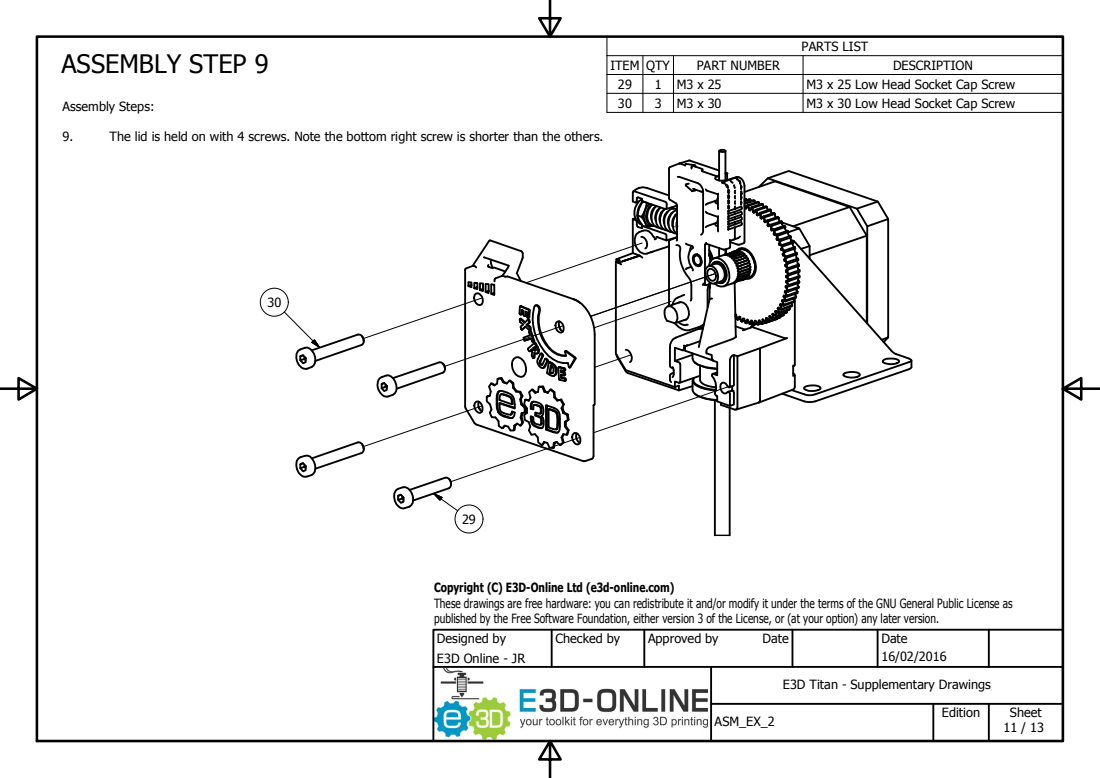
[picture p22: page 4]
ITEM; QTY; PART NUMBER; DESCRIPTION; M3 x 25 Low Head Socket Cap Screw; M3 x 30 Low Head Socket Cap Screw; E3D Online - JR; Designed by; Checked by; Approved by; Date; Edition; Sheet; Assembly Steps:

9. The lid is held on with 4 screws. Note the bottom right screw is shorter than the others.

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

E3D Titan - Supplementary Drawings

# TITAN EXTRENAL DIM'S

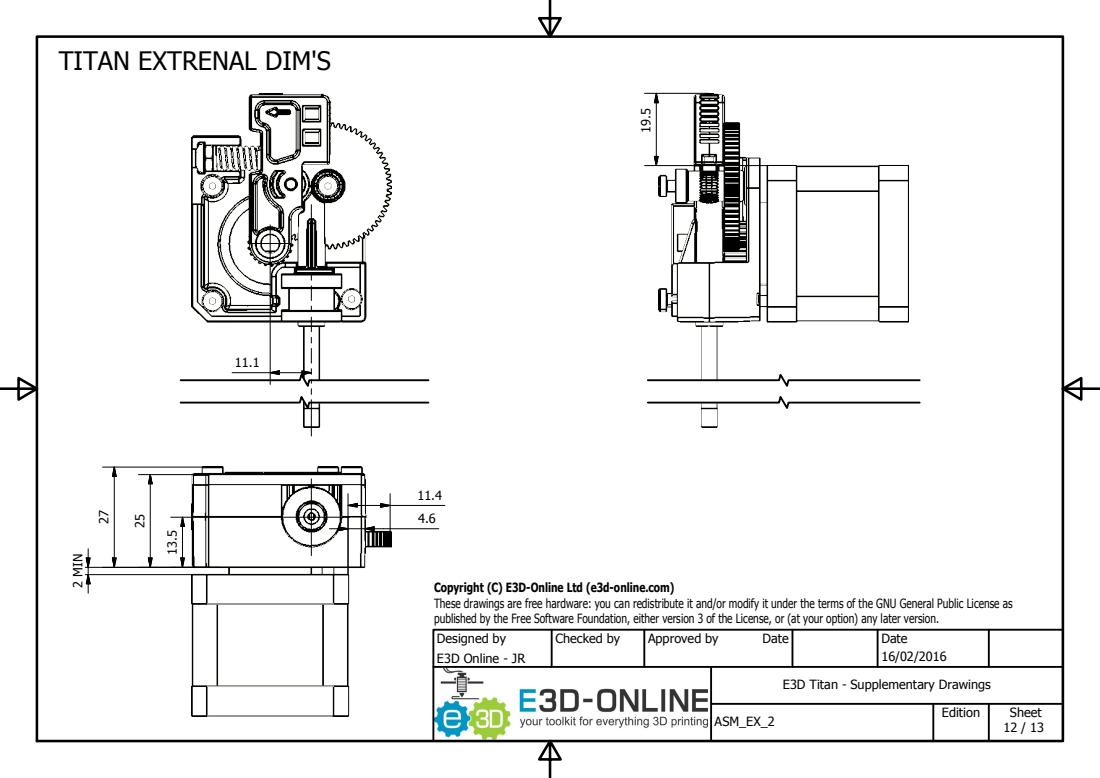
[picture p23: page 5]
E3D Online - JR; Designed by; Checked by; Approved by; Date; Edition; Sheet; 2 MIN

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

E3D Titan - Supplementary Drawings

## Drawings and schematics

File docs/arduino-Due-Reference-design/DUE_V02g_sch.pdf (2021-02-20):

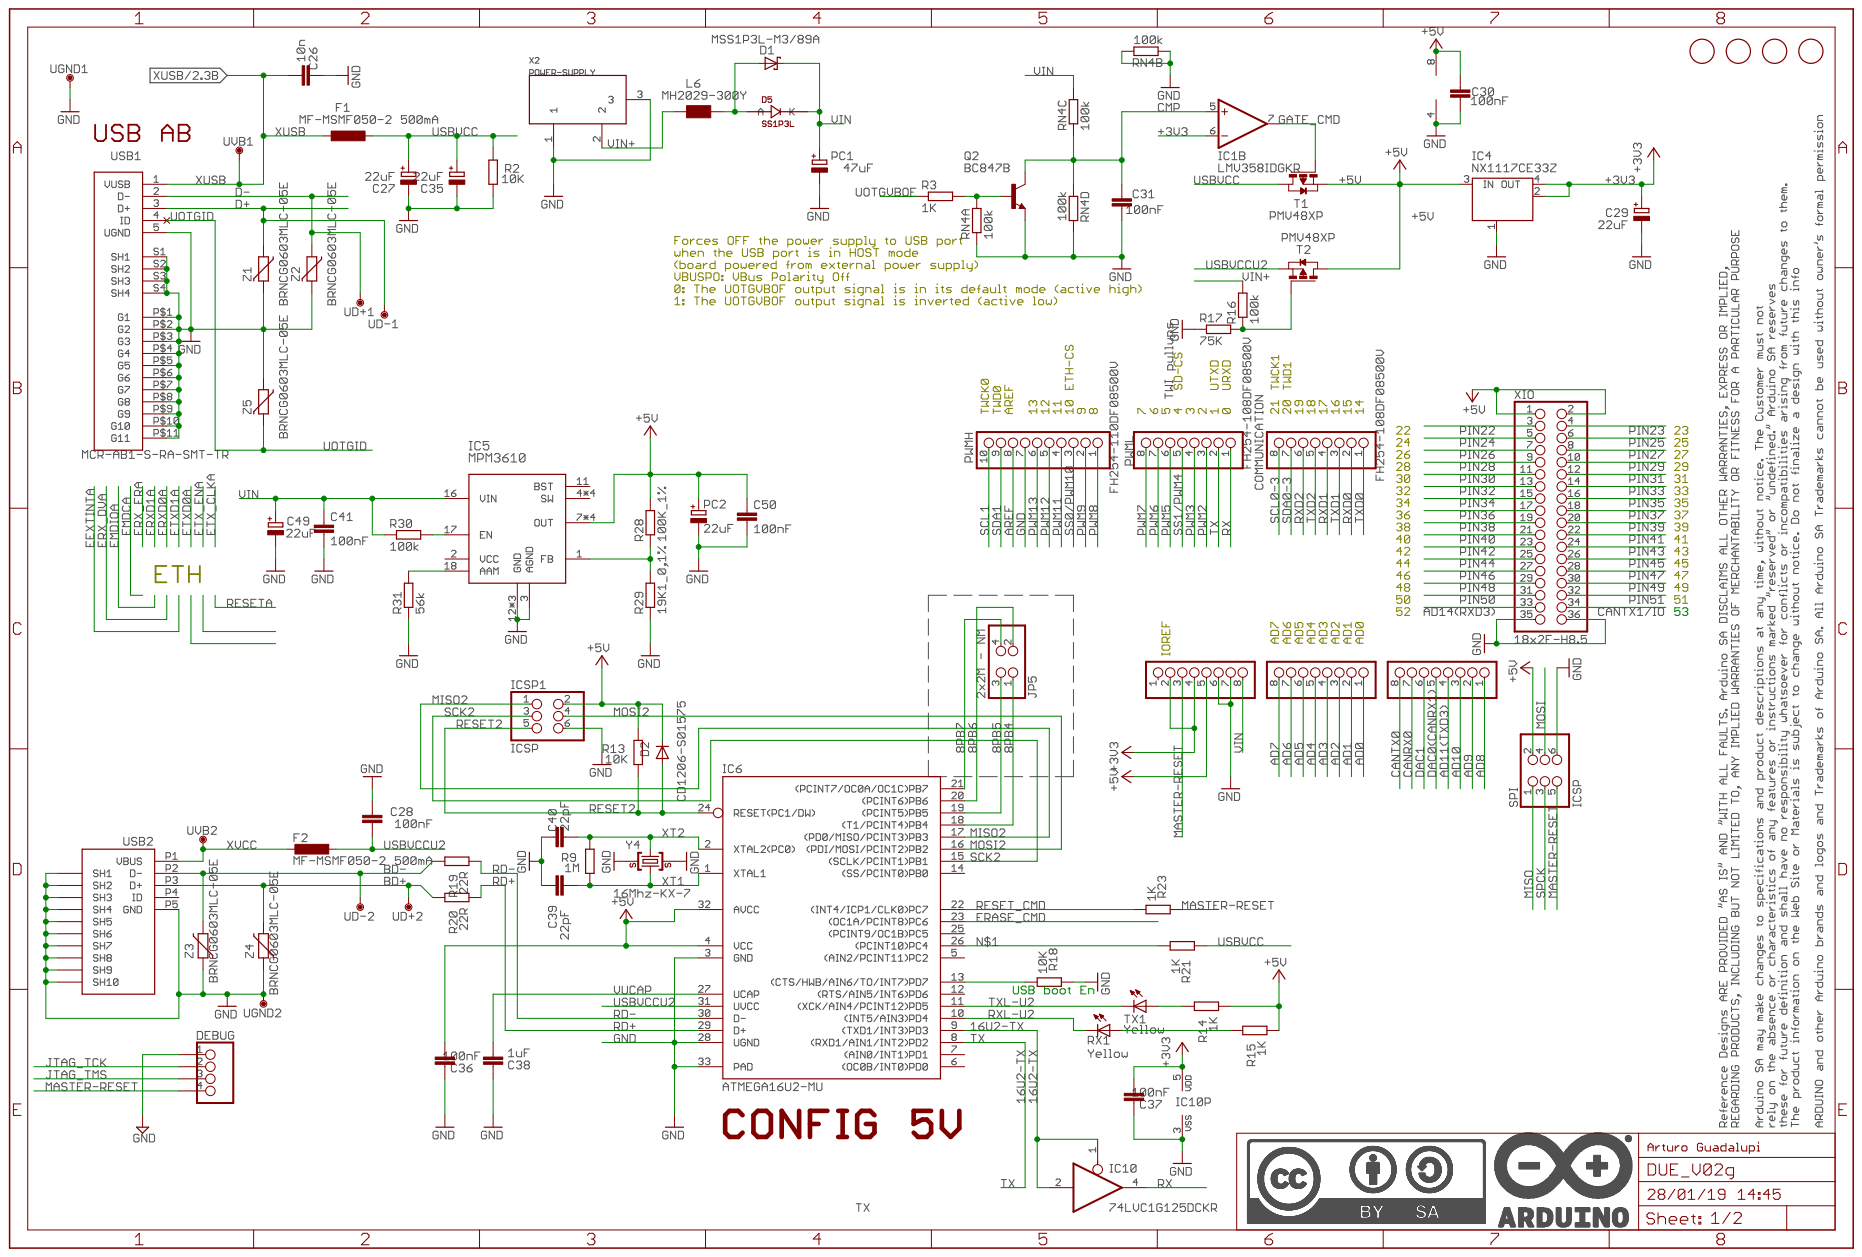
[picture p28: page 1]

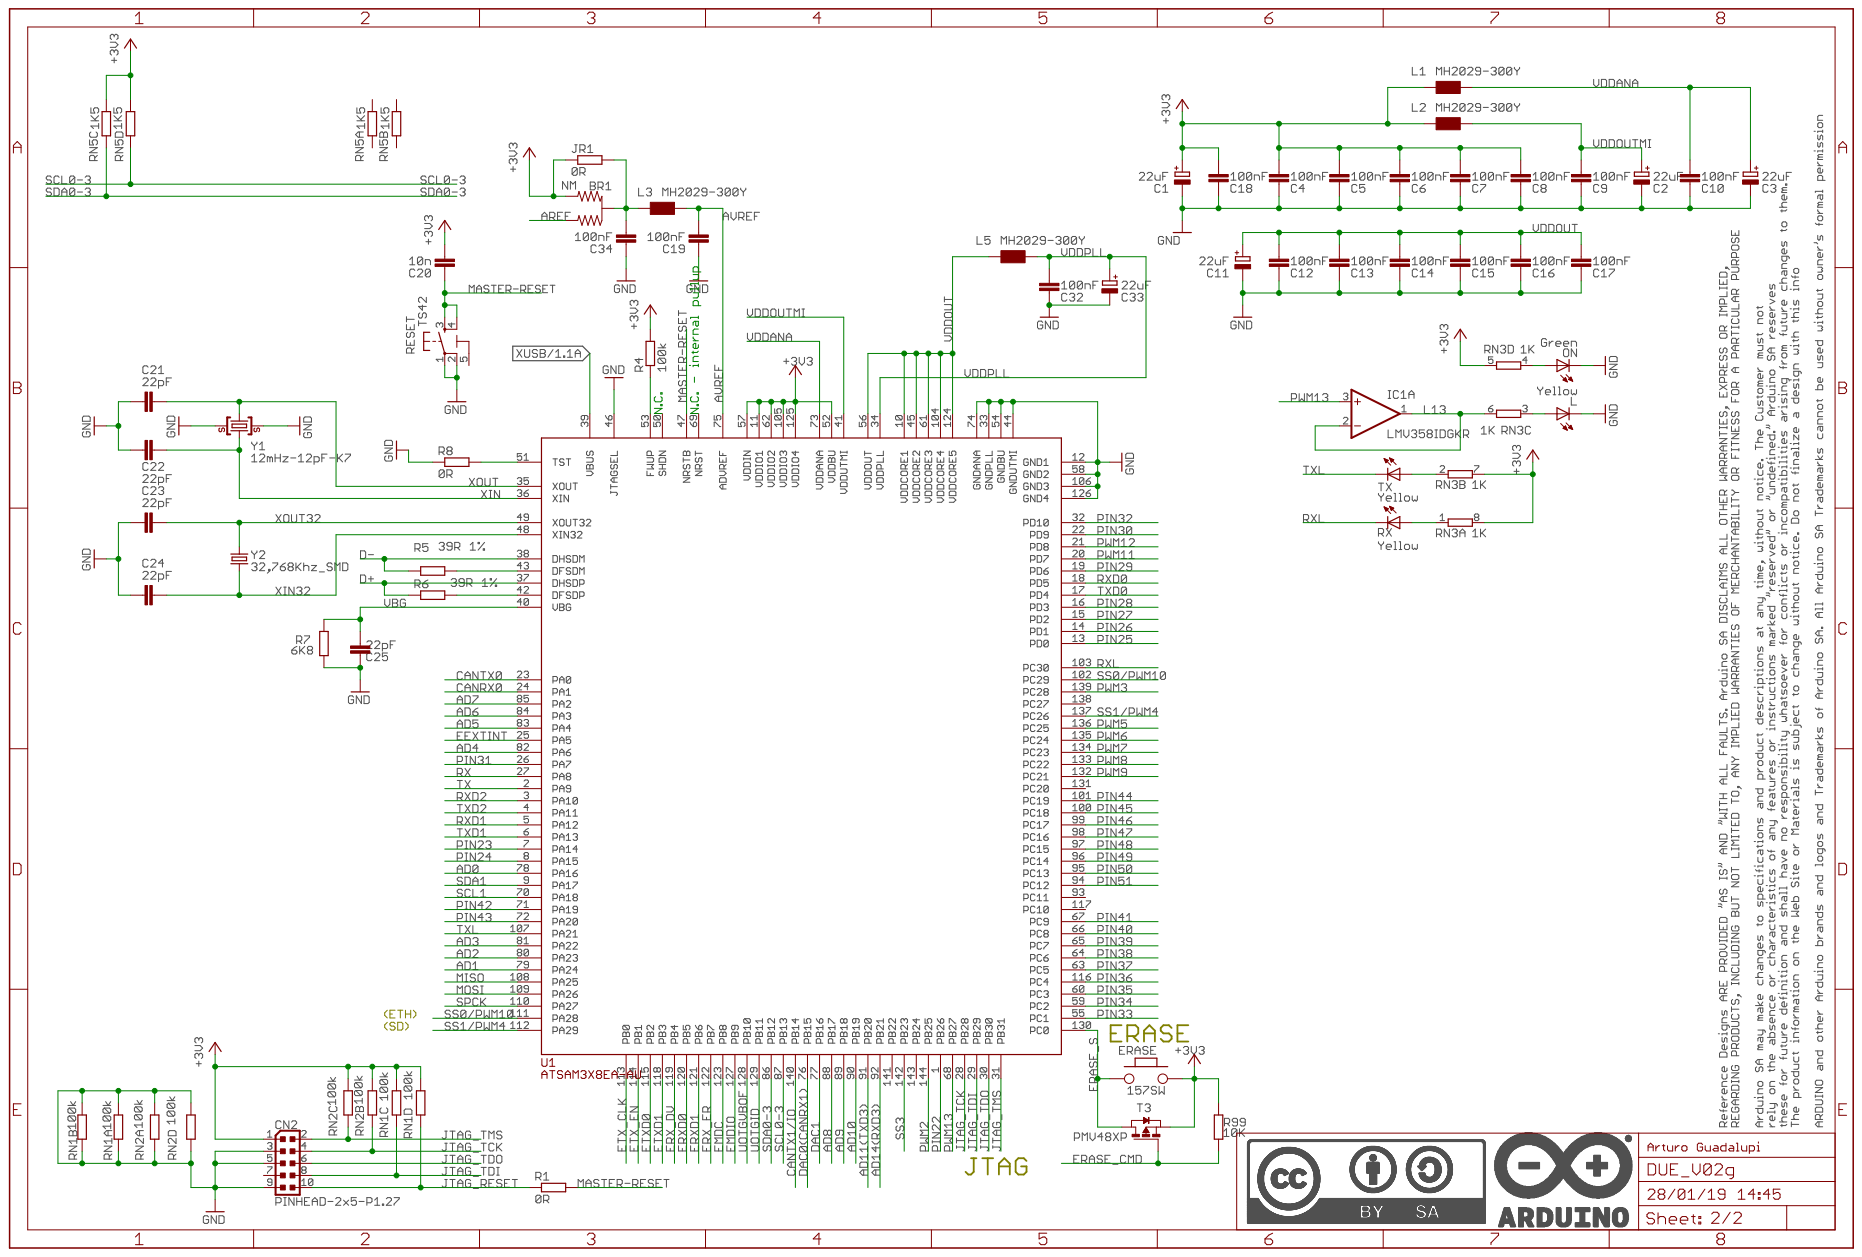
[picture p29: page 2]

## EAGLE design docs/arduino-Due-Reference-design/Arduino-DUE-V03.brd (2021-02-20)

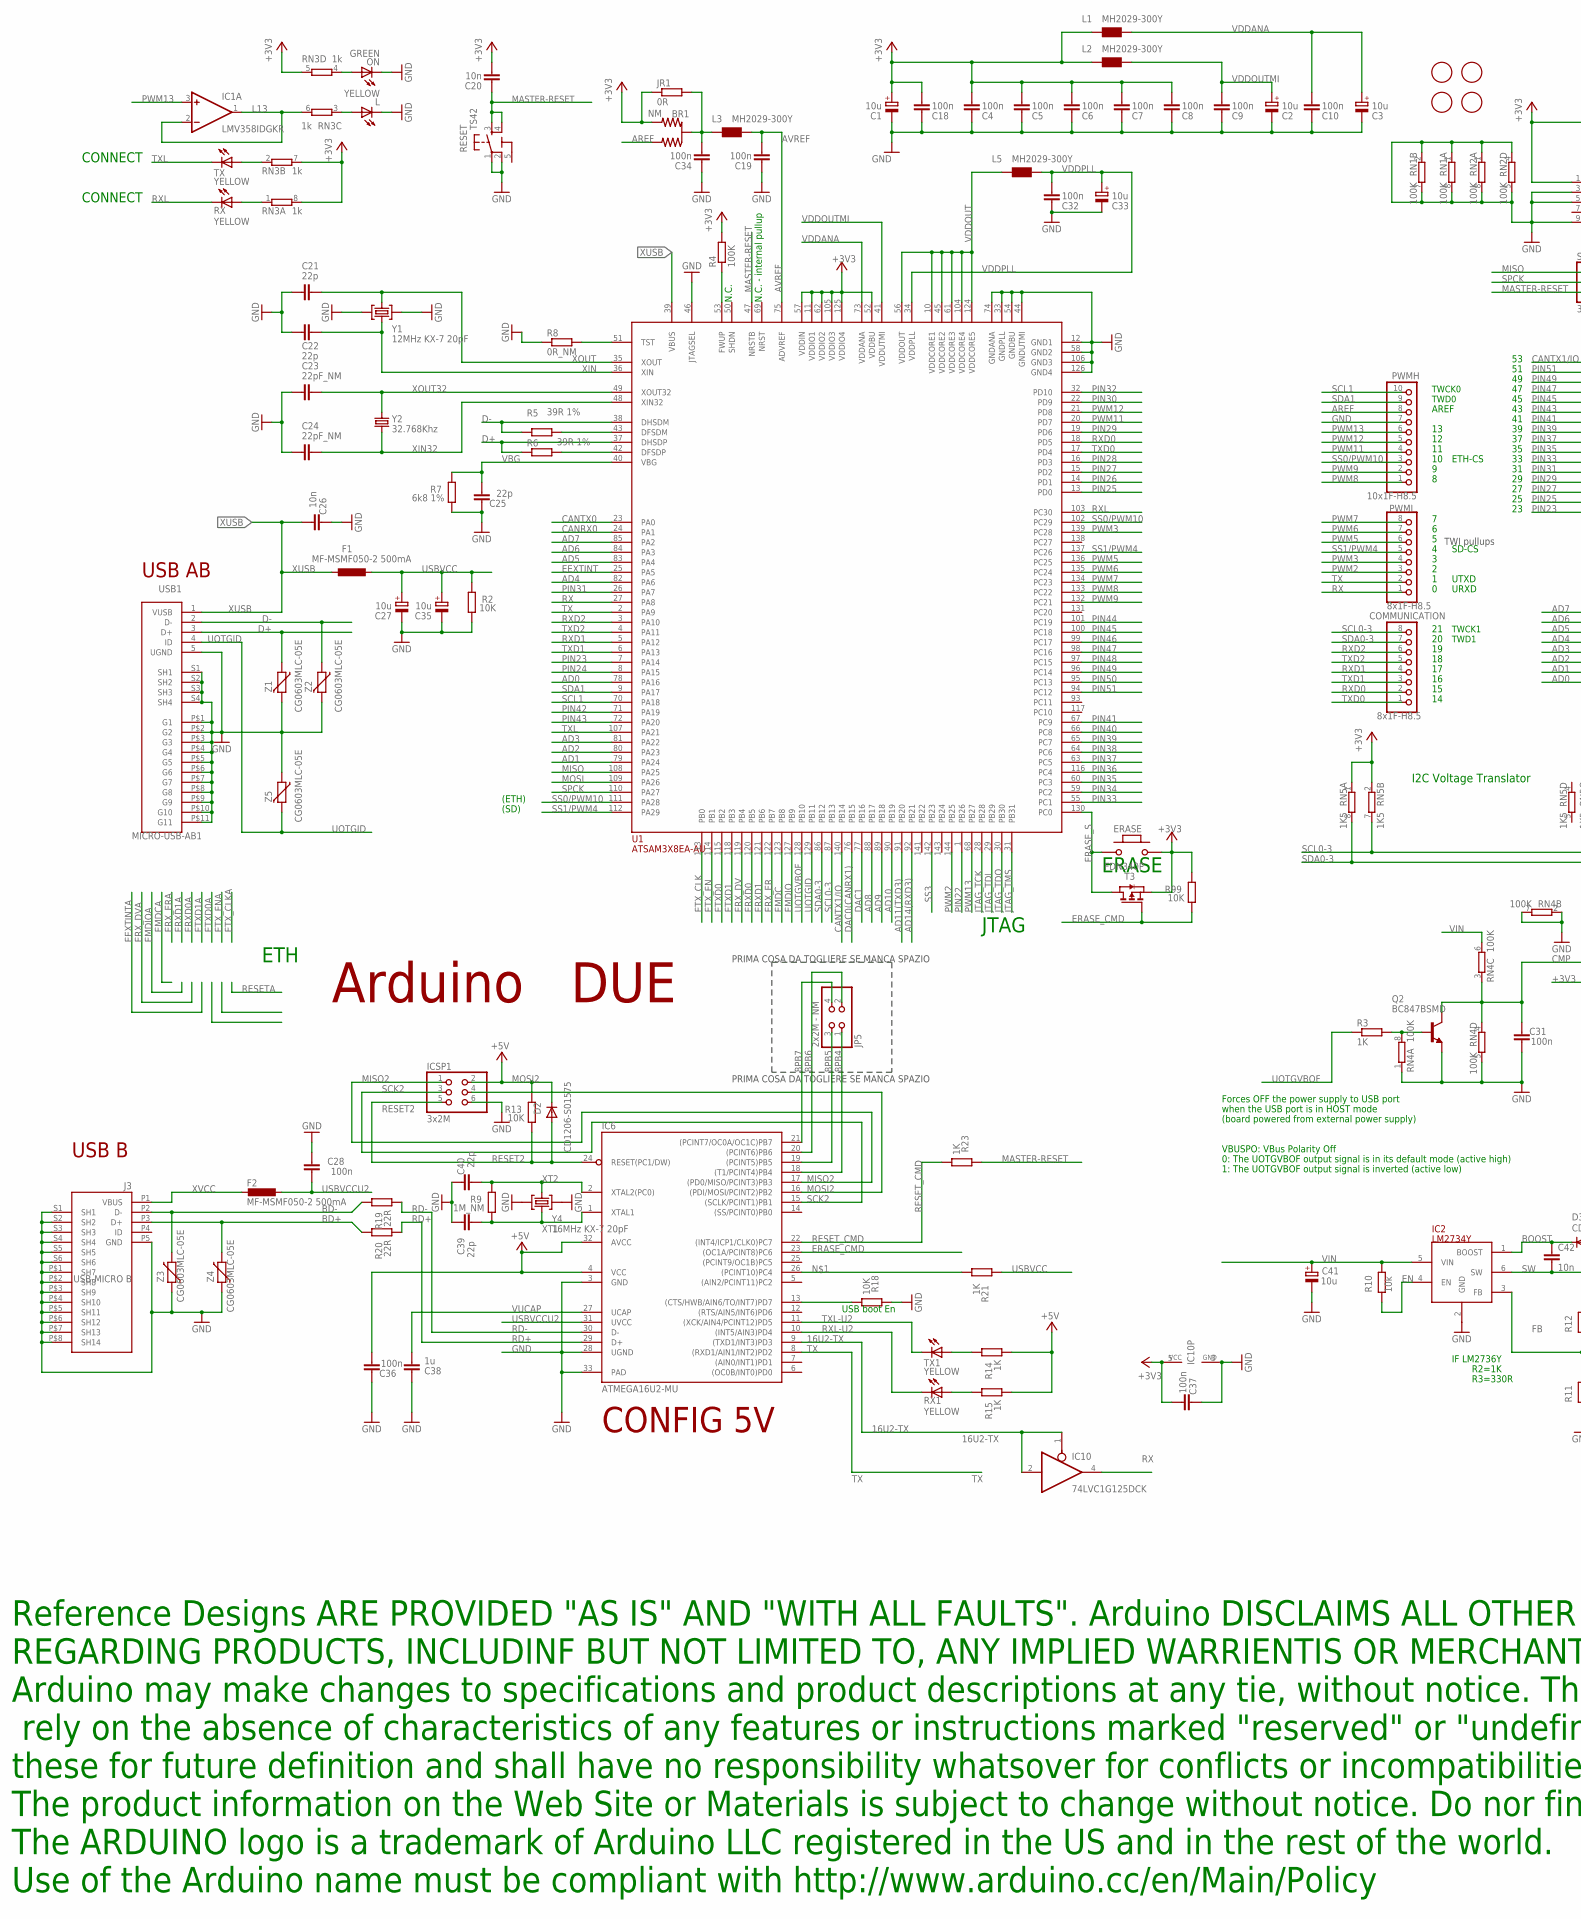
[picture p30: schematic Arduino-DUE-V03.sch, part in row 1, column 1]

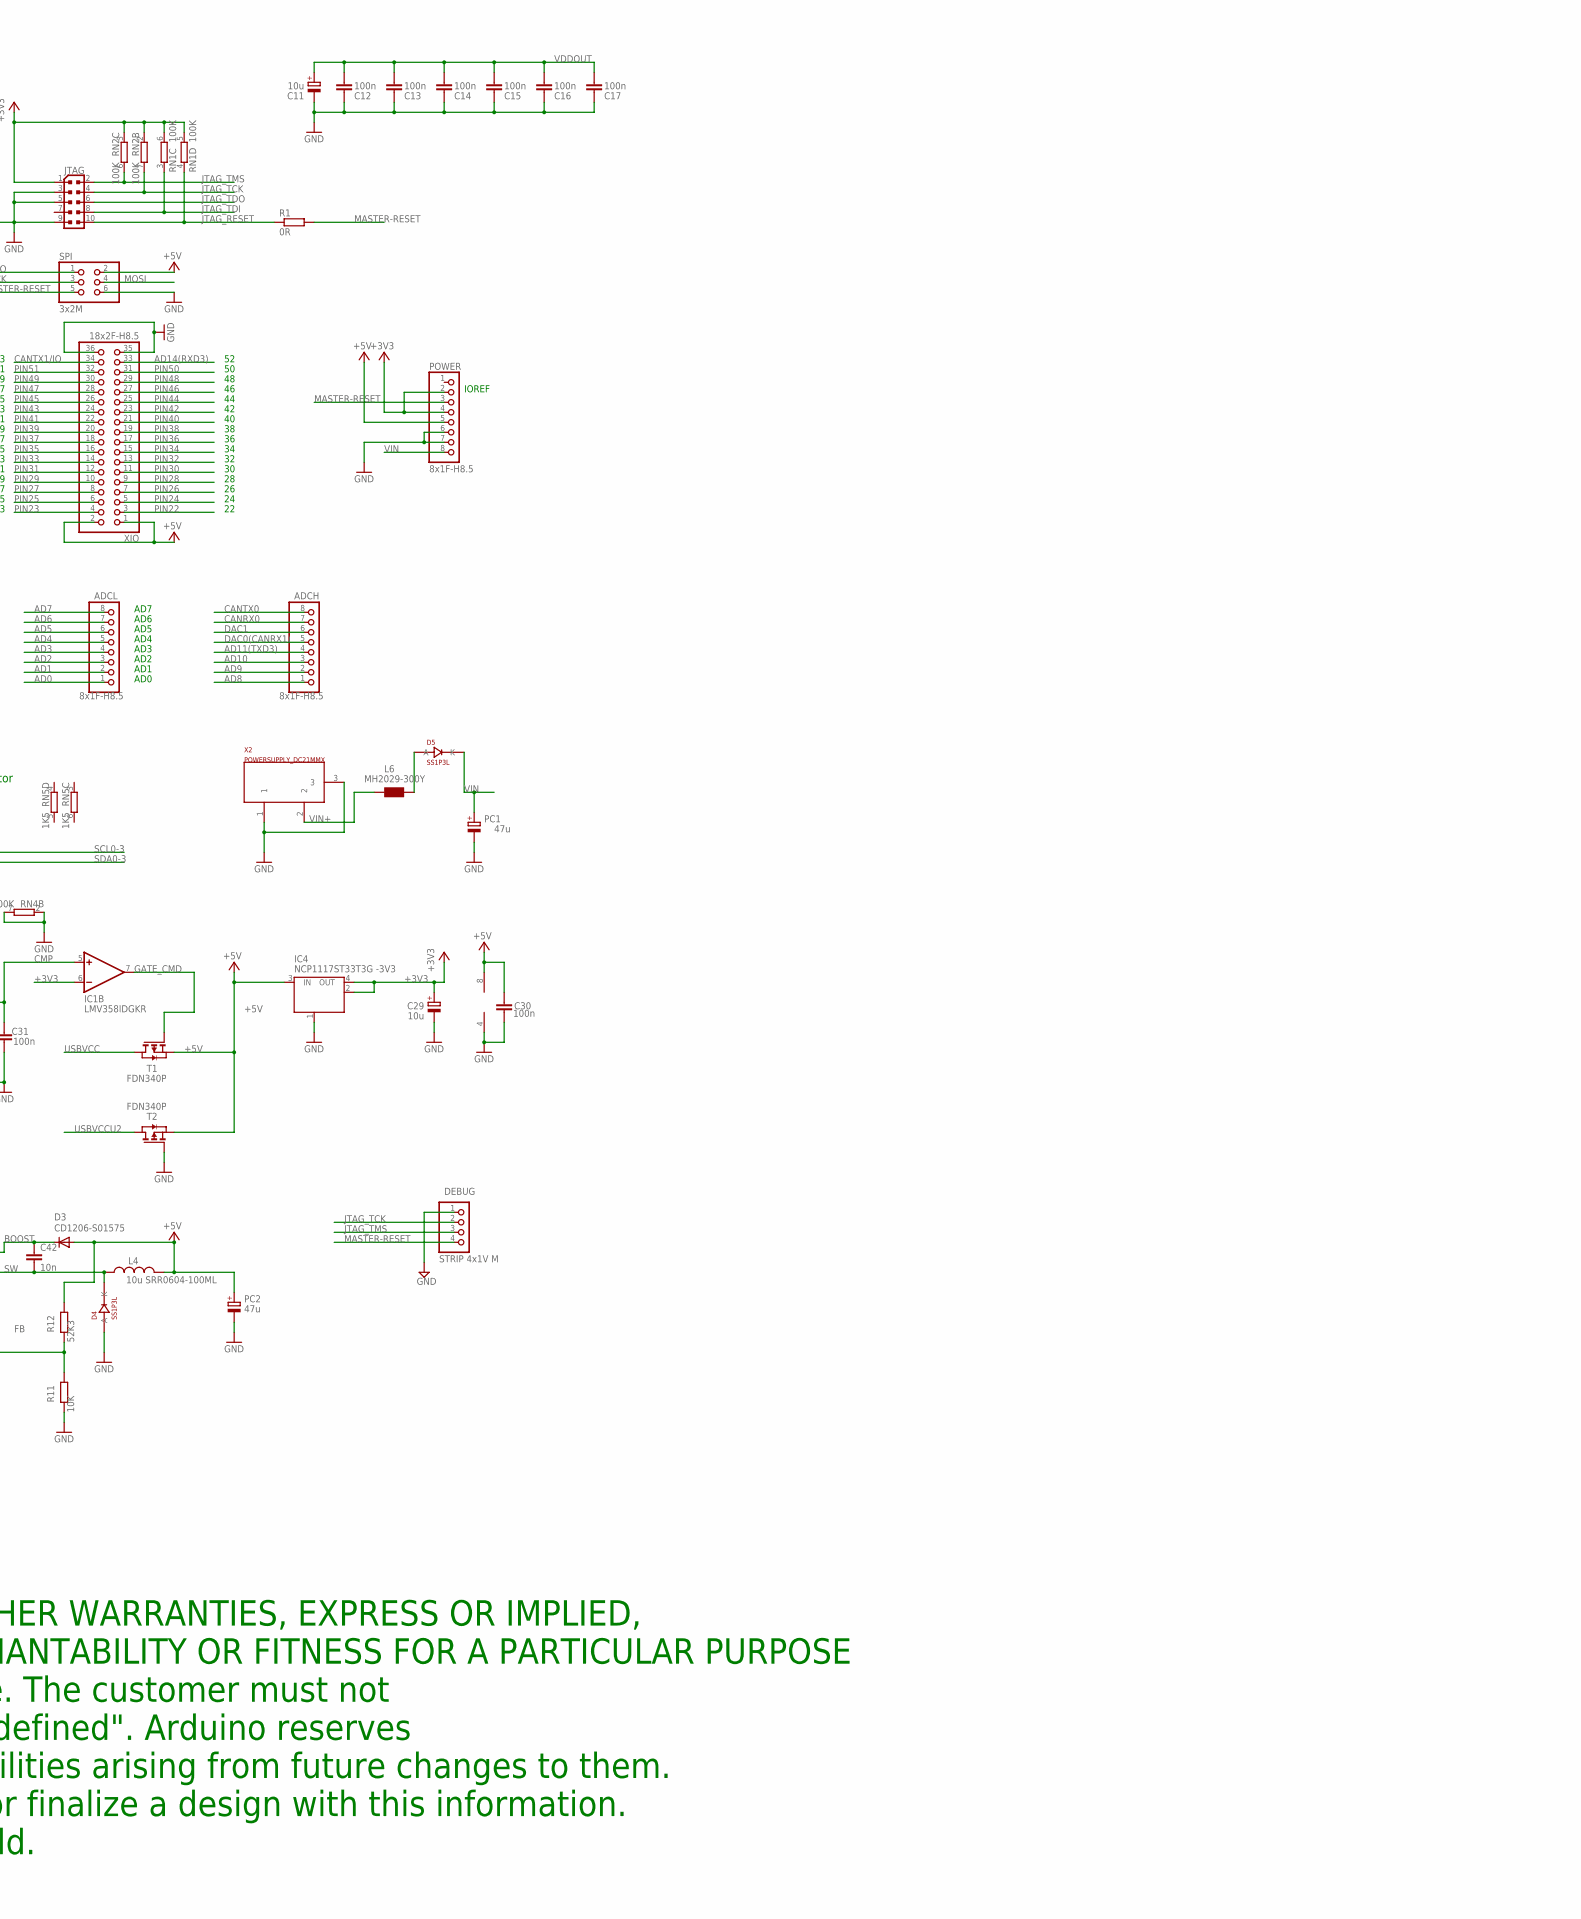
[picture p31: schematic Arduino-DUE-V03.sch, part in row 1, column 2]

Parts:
ADCH: 8x1F-H8.5; 1X08
ADCL: 8x1F-H8.5; 1X08
BR1: NM; J0402
C1, C2, C3, C11, C27, C29, C33, C35, C41: 10u; SMC_B
C4, C5, C6, C7, C8, C9, C10, C12, C13, C14, C15, C16, C17, C18, C19, C28, C30, C31, C32, C34, C36, C37: 100n; C0402
C20, C26: 10n; C0402
C21, C22, C25, C39, C40: 22p; C0402
C23, C24: 22pF_NM; C0402
C38: 1u; C0402
C42: 10n; C0603-ROUND
COMMUNICATION: 8x1F-H8.5; 1X08
D2, D3: CD1206-S01575; MINIMELF
D4, D5: SS1P3L; DO220AAL
DEBUG: STRIP 4x1V M; 1X04
ERASE: MYSMD_PB157; SMD_157SW
F1, F2: MF-MSMF050-2 500mA; L1812
FID1, FID2, FID3, FID4: FIDUCIALMOUNT; FIDUCIA-MOUNT
IC1: LMV358IDGKR; MSOP08
IC2: LM2734Y; SOT23-6
IC4: NCP1117ST33T3G -3V3; SOT223
IC6: ATMEGA16U2-MU; MLF32
IC10: 74LVC1G125DCK; SC70-5
ICSP1: 3x2M; 2X03
J3: USB-MICRO B; CON2_USB_MICRO_B_AT
JP5: 2x2M - NM; 2X02
JR1: 0R; R0402
JTAG: PINHEAD_PINHD-2X5PASSO127; PINHEAD_2X05_127
L: YELLOW; CHIP-LED0805
L1, L2, L3, L5, L6: MH2029-300Y; 0805
L4: 10u SRR0604-100ML; SRR0604
ON: GREEN; CHIP-LED0805
PC1, PC2: 47u; PANASONIC_D
POWER: 8x1F-H8.5; 1X08
PWMH: 10x1F-H8.5; 1X10
PWML: 8x1F-H8.5; 1X08
Q2: BC847BSMD; SOT23
R1: 0R; R0402
R2, R13, R18, R99: 10K; R0402
R3, R14, R15, R21, R23: 1K; R0402
R4: 100K; R0402
R5, R6: 39R 1%; R0402
R7: 6k8 1%; R0603-ROUND
R8: 0R_NM; R0402
R9: 1M_NM; R0402
R10: 10k; R0402
R11: 10K; R0603-ROUND
R12: 52K3; R0603-ROUND
R19, R20: 22R; R0402
RESET: TS42
RN1, RN2, RN4: 100K; CAT16
RN3: 1k; CAY16
RN5: 1K5; CAT16
RX, RX1: YELLOW; CHIP-LED0805
SPI: 3x2M; 2X03
T1, T2, T3: FDN340P; SOT-23
TX, TX1: YELLOW; CHIP-LED0805
U1: ATSAM3X8EA-AU; LQFP144
USB1: MICRO-USB-AB1; MCR-AB1-S-RA-SMT
X2: POWERSUPPLY_DC21MMX; POWERSUPPLY_DC-21MM
XIO: 18x2F-H8.5; 2X18
Y1: 12MHz KX-7 20pF; CRYSTAL-3.2-2.5
Y2: 32.768Khz; RESONATOR_EPSON_FC_145
Y4: 16MHz KX-7 20pF; CRYSTAL-3.2-2.5
Z1, Z2, Z3, Z4, Z5: CG0603MLC-05E; CT/CN0603

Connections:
5-GND: RESET.5 (5-GND)
8PB4: IC6.18 ((T1/PCINT4)PB4), JP5.1
8PB5: IC6.19 ((PCINT5)PB5), JP5.3
8PB6: IC6.20 ((PCINT6)PB6), JP5.2
8PB7: IC6.21 ((PCINT7/OC0A/OC1C)PB7), JP5.4
16U2-TX: IC6.9 ((TXD1/INT3)PD3), IC10.1 (OE), IC10.2 (I)
+3V3: BR1.3 (2), C1.+, C4.2, C5.2, C6.2, C7.2, C8.2, C18.2, C20.2, C29.+, C37.1, ERASE.1, IC1.6 (-IN), IC4.2 (OUT), IC4.4 (OUT), IC10.5 (VCC), JR1.1, JTAG.1, L1.1, L2.1, POWER.2, POWER.4, R4.2, R99.2, RN1.5 (2), RN1.6 (2), RN2.2 (1), RN2.3 (1), RN3.5 (2), RN3.7 (2), RN3.8 (2), RN5.1, RN5.2 (1), T3.2 (S), U1.11 (VDDIO1), U1.52 (VDDBU), U1.57 (VDDIN), U1.62 (VDDIO2), U1.105 (VDDIO3), U1.125 (VDDIO4)
+5V: C30.2, C36.1, D2.C, D3.A, IC1.8 (V+), IC4.3 (IN), IC6.4 (VCC), IC6.32 (AVCC), ICSP1.2, L4.P$2 (2), PC2.+, POWER.5, R12.1, R13.2, R14.1, R15.1, SPI.2, T1.2 (S), T2.2 (S), XIO.1, XIO.2
AD0: ADCL.1, U1.78 (PA16)
AD1: ADCL.2, U1.79 (PA24)
AD2: ADCL.3, U1.80 (PA23)
AD3: ADCL.4, U1.81 (PA22)
AD4: ADCL.5, U1.82 (PA6)
AD5: ADCL.6, U1.83 (PA4)
AD6: ADCL.7, U1.84 (PA3)
AD7: ADCL.8, U1.85 (PA2)
AD8: ADCH.1, U1.88 (PB17)
AD9: ADCH.2, U1.89 (PB18)
AD10: ADCH.3, U1.90 (PB19)
AD11(TXD3): ADCH.4, U1.91 (PB20)
AD14(RXD3): U1.92 (PB21), XIO.33
AREF: BR1.1, PWMH.8
AVREF: C19.2, L3.2, U1.75 (ADVREF)
AVREFL: BR1.2 (C), C34.2, JR1.2, L3.1
BD+: J3.P3 (D+), R20.2, Z4.2
BD-: J3.P2 (D-), R19.2, Z3.2
BOOST: C42.1, D3.C, IC2.1 (BOOST)
CANRX0: ADCH.7, U1.24 (PA1)
CANTX0: ADCH.8, U1.23 (PA0)
CANTX1/IO: U1.140 (PB14), XIO.34
CMP: C31.2, IC1.5 (+IN), Q2.3 (C), RN4.3 (1), RN4.4 (1)
D+: R6.1, U1.37 (DHSDP), USB1.3 (D+), Z1.1
D-: R5.1, U1.38 (DHSDM), USB1.2 (D-), Z2.1
DAC0(CANRX1): ADCH.5, U1.76 (PB15)
DAC1: ADCH.6, U1.77 (PB16)
DTR: IC6.13 ((CTS/HWB/AIN6/TO/INT7)PD7), R18.1
EEXTINT: U1.25 (PA5)
EMDC: U1.123 (PB8)
EMDIO: U1.127 (PB9)
EN: IC2.4 (EN), R10.2
ERASE_CMD: IC6.23 ((OC1A/PCINT8)PC6), R99.1, T3.3 (G)
ERASE_S: ERASE.2, T3.1 (D), U1.130 (PC0)
ERXD0: U1.120 (PB5)
ERXD1: U1.121 (PB6)
ERX_DV: U1.119 (PB4)
ERX_ER: U1.122 (PB7)
ETXD0: U1.115 (PB2)
ETXD1: U1.118 (PB3)
ETX_CLK: U1.113 (PB0)
ETX_EN: U1.114 (PB1)
FB: IC2.3 (FB), R11.1, R12.2
GATE_CMD: IC1.7 (OUT), T1.3 (G)
GND: C1.-, C2.-, C3.-, C4.1, C5.1, C6.1, C7.1, C8.1, C9.1, C10.1, C11.-, C12.1, C13.1, C14.1, C15.1, C16.1, C17.1, C18.1, C19.1, C21.2, C22.2, C23.2, C24.2, C25.2, C26.2, C27.-, C28.2, C29.-, C30.1, C31.1, C32.1, C33.-, C34.1, C35.-, C36.2, C37.2, C38.2, C39.2, C40.2, C41.-, D4.P$2 (A), DEBUG.1, IC1.4 (V-), IC2.2 (GND), IC4.1 (GND/ADJ), IC6.3 (GND), IC6.28 (UGND), IC6.33 (PAD), IC10.3 (GND), ICSP1.6, J3.P5 (GND), J3.P$1 (SH7), J3.P$2 (SH8), J3.P$3 (SH9), J3.P$4 (SH10), J3.P$5 (SH11), J3.P$6 (SH12), J3.P$7 (SH13), J3.P$8 (SH14), J3.S1 (SH1), J3.S2 (SH2), J3.S3 (SH3), J3.S4 (SH4), J3.S5 (SH5), J3.S6 (SH6), JTAG.3, JTAG.5, JTAG.9, L.C, ON.C, PC1.-, PC2.-, POWER.6, POWER.7, PWMH.7, Q2.2 (E), R2.1, R7.1, R8.1, R11.2, R18.2, RESET.1, RESET.2, RN1.1, RN1.2 (1), RN1.7 (2), RN1.8 (2), RN2.1, RN2.4 (1), RN2.5 (2), RN2.8 (2), RN4.1, RN4.2 (1), RN4.5 (2), RN4.7 (2), SPI.6, T2.3 (G), U1.12 (GND1), U1.33 (GNDPLL), U1.44 (GNDUTMI), U1.46 (JTAGSEL), U1.54 (GNDBU), U1.58 (GND2), U1.74 (GNDANA), U1.106 (GND3), U1.126 (GND4), USB1.5 (UGND), USB1.P$1 (G1), USB1.P$2 (G2), USB1.P$3 (G3), USB1.P$4 (G4), USB1.P$5 (G5), USB1.P$6 (G6), USB1.P$7 (G7), USB1.P$8 (G8), USB1.P$9 (G9), USB1.P$10 (G10), USB1.P$11 (G11), USB1.S1 (SH1), USB1.S2 (SH2), USB1.S3 (SH3), USB1.S4 (SH4), X2.1, X2.3, XIO.35, XIO.36, Y1.2 (GND), Y1.4 (GND), Y4.2 (GND), Y4.4 (GND), Z1.2, Z2.2, Z3.1, Z4.1, Z5.1
JTAG_RESET: JTAG.10, R1.1, RN1.4 (1)
JTAG_TCK: DEBUG.2, JTAG.4, RN2.7 (2), U1.28 (PB28)
JTAG_TDI: JTAG.8, RN1.3 (1), U1.29 (PB29)
JTAG_TDO: JTAG.6, U1.30 (PB30)
JTAG_TMS: DEBUG.3, JTAG.2, RN2.6 (2), U1.31 (PB31)
L13: IC1.1 (OUT), IC1.2 (-IN), RN3.6 (2)
MASTER-RESET: C20.1, DEBUG.4, POWER.3, R1.2, R23.2, RESET.3, RESET.4, SPI.5, U1.47 (NRSTB)
MISO: SPI.1, U1.108 (PA25)
MISO2: IC6.17 ((PD0/MISO/PCINT3)PB3), ICSP1.1
MOSI: SPI.4, U1.109 (PA26)
MOSI2: IC6.16 ((PDI/MOSI/PCINT2)PB2), ICSP1.4
unnamed: IC6.26 ((PCINT10)PC4), R21.1
unnamed: L.A, RN3.3 (1)
unnamed: ON.A, RN3.4 (1)
unnamed: R15.2, RX1.A
unnamed: R8.2, U1.51 (TST)
unnamed: Q2.1 (B), R3.2, RN4.8 (2)
unnamed: R4.1, U1.53 (FWUP)
unnamed: D5.P$2 (A), L6.1
unnamed: R5.2, U1.43 (DFSDM)
unnamed: R6.2, U1.42 (DFSDP)
unnamed: R14.2, TX1.A
unnamed: RN3.1, RX.A
unnamed: RN3.2 (1), TX.A
PIN22: U1.1 (PB26), XIO.3
PIN23: U1.7 (PA14), XIO.4
PIN24: U1.8 (PA15), XIO.5
PIN25: U1.13 (PD0), XIO.6
PIN26: U1.14 (PD1), XIO.7
PIN27: U1.15 (PD2), XIO.8
PIN28: U1.16 (PD3), XIO.9
PIN29: U1.19 (PD6), XIO.10
PIN30: U1.22 (PD9), XIO.11
PIN31: U1.26 (PA7), XIO.12
PIN32: U1.32 (PD10), XIO.13
PIN33: U1.55 (PC1), XIO.14
PIN34: U1.59 (PC2), XIO.15
PIN35: U1.60 (PC3), XIO.16
PIN36: U1.116 (PC4), XIO.17
PIN37: U1.63 (PC5), XIO.18
PIN38: U1.64 (PC6), XIO.19
PIN39: U1.65 (PC7), XIO.20
PIN40: U1.66 (PC8), XIO.21
PIN41: U1.67 (PC9), XIO.22
PIN42: U1.71 (PA19), XIO.23
PIN43: U1.72 (PA20), XIO.24
PIN44: U1.101 (PC19), XIO.25
PIN45: U1.100 (PC18), XIO.26
PIN46: U1.99 (PC17), XIO.27
PIN47: U1.98 (PC16), XIO.28
PIN48: U1.97 (PC15), XIO.29
PIN49: U1.96 (PC14), XIO.30
PIN50: U1.95 (PC13), XIO.31
PIN51: U1.94 (PC12), XIO.32
PWM2: PWML.3, U1.144 (PB25)
PWM3: PWML.4, U1.139 (PC28)
PWM5: PWML.6, U1.136 (PC25)
PWM6: PWML.7, U1.135 (PC24)
PWM7: PWML.8, U1.134 (PC23)
PWM8: PWMH.1, U1.133 (PC22)
PWM9: PWMH.2, U1.132 (PC21)
PWM11: PWMH.4, U1.20 (PD7)
PWM12: PWMH.5, U1.21 (PD8)
PWM13: IC1.3 (+IN), PWMH.6, U1.68 (PB27)
RD+: IC6.29 (D+), R20.1
RD-: IC6.30 (D-), R19.1
RESET2: D2.A, IC6.24 (RESET(PC1/DW)), ICSP1.5, R13.1
RESET_CMD: IC6.22 ((INT4/ICP1/CLK0)PC7), R23.1
RX: IC10.4 (O), PWML.1, U1.27 (PA8)
RXD0: COMMUNICATION.2, U1.18 (PD5)
RXD1: COMMUNICATION.4, U1.5 (PA12)
RXD2: COMMUNICATION.6, U1.3 (PA10)
RXL: RX.C, U1.103 (PC30)
RXL-U2: IC6.10 ((INT5/AIN3)PD4), RX1.C
SCK2: IC6.15 ((SCLK/PCINT1)PB1), ICSP1.3
SCL0-3: COMMUNICATION.8, RN5.7 (2), U1.87 (PB13)
SCL1: PWMH.10, U1.70 (PA18)
SDA0-3: COMMUNICATION.7, RN5.8 (2), U1.86 (PB12)
SDA1: PWMH.9, U1.9 (PA17)
SPCK: SPI.3, U1.110 (PA27)
SS0/PWM10: PWMH.3, U1.102 (PC29), U1.111 (PA28)
SS1/PWM4: PWML.5, U1.112 (PA29), U1.137 (PC26)
SS3: U1.142 (PB23)
SW: C42.2, D4.P$1 (K), IC2.6 (SW), L4.P$1 (1)
TX: IC6.8 ((RXD1/AIN1/INT2)PD2), PWML.2, U1.2 (PA9)
TXD0: COMMUNICATION.1, U1.17 (PD4)
TXD1: COMMUNICATION.3, U1.6 (PA13)
TXD2: COMMUNICATION.5, U1.4 (PA11)
TXL: TX.C, U1.107 (PA21)
TXL-U2: IC6.11 ((XCK/AIN4/PCINT12)PD5), TX1.C
UOTGID: U1.129 (PB11), USB1.4 (ID), Z5.2
UOTGVBOF: R3.1, U1.128 (PB10)
USBVCC: C27.+, C35.+, F1.1, R2.2, R21.2, T1.1 (D)
USBVCCU2: C28.1, F2.1, IC6.31 (UVCC), T2.1 (D)
VBG: C25.1, R7.2, U1.40 (VBG)
VDDANA: C3.+, C10.2, L1.2, U1.73 (VDDANA)
VDDOUT: C11.+, C12.2, C13.2, C14.2, C15.2, C16.2, C17.2, L5.1, U1.10 (VDDCORE1), U1.45 (VDDCORE2), U1.56 (VDDOUT), U1.61 (VDDCORE3), U1.104 (VDDCORE4), U1.124 (VDDCORE5)
VDDOUTMI: C2.+, C9.2, L2.2, U1.41 (VDDUTMI)
VDDPLL: C32.2, C33.+, L5.2, U1.34 (VDDPLL)
VIN: C41.+, D5.P$1 (K), IC2.5 (VIN), PC1.+, POWER.8, R10.1, RN4.6 (2)
VIN+: L6.2, X2.2
VUCAP: C38.1, IC6.27 (UCAP)
XIN: C22.1, U1.36 (XIN), Y1.1 (C1)
XIN32: C24.1, U1.48 (XIN32), Y2.P$2 (2)
XOUT: C21.1, U1.35 (XOUT), Y1.3 (C2)
XOUT32: C23.1, U1.49 (XOUT32), Y2.P$1 (1)
XT1: C39.1, IC6.1 (XTAL1), R9.1, Y4.1 (C1)
XT2: C40.1, IC6.2 (XTAL2(PC0)), R9.2, Y4.3 (C2)
XUSB: C26.1, F1.2, U1.39 (VBUS), USB1.1 (VUSB)
XVCC: F2.2, J3.P1 (VBUS)

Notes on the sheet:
TWI pullups
TWCK1
TWD1
IOREF
TWCK0
TWD0
AD1
AD2
AD3
AD4
AD5
AD6
AD0
USB AB
AREF
AD7
SD-CS
Forces OFF the power supply to USB port
when the USB port is in HOST mode
(board powered from external power supply)
N.C.
JTAG
ERASE
CONNECT
VBUSPO: VBus Polarity Off
0: The UOTGVBOF output signal is in its default mode (active high)
1: The UOTGVBOF output signal is inverted (active low)
ETH
UTXD
URXD
(ETH)
(SD)
ETH-CS
I2C Voltage Translator
USB boot En
IF LM2736Y
R2=1K
R3=330R
PRIMA COSA DA TOGLIERE SE MANCA SPAZIO
CONFIG 5V

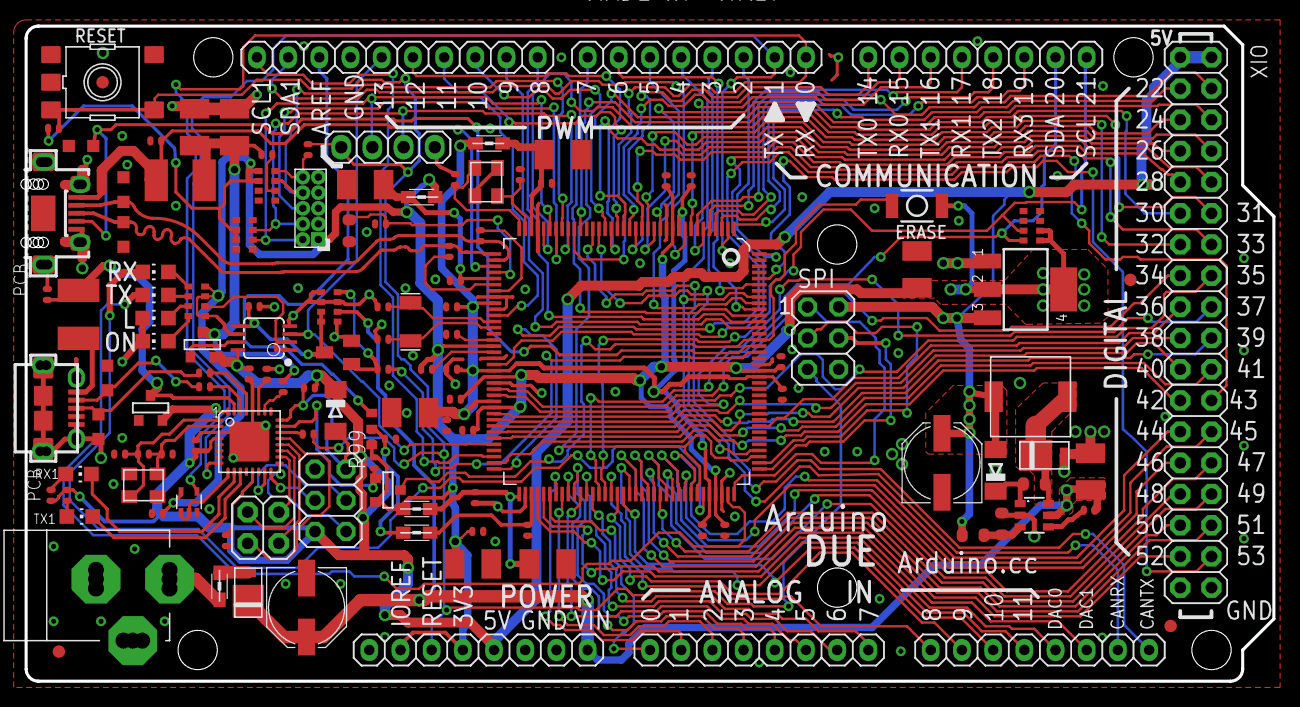
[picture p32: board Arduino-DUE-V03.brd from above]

Board: 2 copper layers, 101.6 x 53.3 mm, 129 parts (0 on the bottom side), 150 nets.

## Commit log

2020-12-06 change dims for all 400mm rod, y-carrage for 170mm hot plate hole spacing and 4m screws, belt offset for 12mm pully and idler
    restore gitignore
    [B.O.M - iTopie RepRap - MDF16.xlsx, config.scad]
2020-12-11 reduce y-rod play from 20mm to 6mm
    [config.scad]
2020-12-13 add pockets to use max 20mm long screws, add reference border
    [config.scad, main.scad, vertical_plate.scad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]
2020-12-13 stl updates pending
2021-02-20 scad for end idler and motor on x carrage
    referece docs, error corrections
    flex extruder adapter, y-idler
    add xcarrage for areo style mount
    electrical case
    Itopie400+ largely working with reference materail and progress shots
    [3DPNFilHoldBrace.stl, 3DPNFilHoldGuide.stl, 3DPNFilHoldRoller.stl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]
2021-02-21 move probe down 12mm and bit closer to nozel
    [titan_aero_mount400v0.scad]
2021-02-27 new titan areo hot end mount, uses full bed, w. probe & wire support, clip-on wire guide for x-motor
    [titan_aero_mount400v0.scad, titan_aero_mount400v0_cowling.stl, x-cable_guid.scad]
2021-02-27 updates to referenced Marlin repo
2021-02-27 cleanup and update mount part
    [elec_case.stl, titan_aero_mount400v0.stl]
2021-02-28 Update README.md
    Printer is working.
2021-03-05 add y-spacer for homing
    [clip-on-endstop-spacer.scad, clip-on-endstop-spacer.stl]
2021-03-09 add cut-out option in horizontal plate to make air chamber enclosure
    [horizontal_plate.scad]
2021-03-09 add bed test print for level bed
    add bed test print for level bed 2
    [bed_test.scad, bed_test.stl]
2021-03-09 gasket to hold oring for damping noise
    gasket to hold oring for damping noise 2
    [damper_fan_mount.scad, damper_fan_mount.stl]
2021-03-09 progress on part cooling ducts
    [titan_aero_mount400v0.scad]

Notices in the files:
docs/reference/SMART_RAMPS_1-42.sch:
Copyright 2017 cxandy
